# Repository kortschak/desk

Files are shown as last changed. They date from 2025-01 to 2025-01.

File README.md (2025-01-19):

# desk controller

This is the code and hardware details for a WiFi/Bluetooth Man-in-the-Middle controller for an AOKE Wistopht WP-CB01-901 32.5 standing desk controller.

The project is educational only. If you do not know what you are doing, do not use this document as a how-to. Using the device described here will almost certainly void your desk's warranty.

## Controls

### HTTP

The controller will be visible as `desk` in your LAN. It exposes HTTP endpoints.

Endpoints:
- `PUT /move_to/?position=<pos>`: `<pos>` is `1`, `2`, `3` or `4` corresponding to the programmed memory heights for the desk
- `GET /height/`: returns height of desk

Due to the protocol used by the desk, the height endpoint may return the last programmed memory height instead of the actual desk height.

### Bluetooth

The controller will advertise a service with your provided name and UUIDs. The `move_to` characteristic is read/write allowing you to move to the programmed memory heights for the desk, and a read `height` characteristic that will give a string showing the height of the desk. If the value is "0", it is not yet known to the remote controller.

## Building

Install `tinygo` version 0.34.0+ and then:

If building for HTTP control, write your SSID into wifi/ssid.text and your WiFi password into wifi/password.text. Do not add a final newline to the files.

If building for Bluetooth control, write single word name into a file advertise_name.text to name the Bluetooth service and then provide UUIDs for the service and exposed characteristics: `uuidgen >service.uuid`, `uuidgen >move_to.uuid` and `uuidgen >height.uuid` (confirm that the UUIDs do not collide with any that are already being used locally).

Use `tinygo flash` at the root of the repo with the target Raspberry Pi Pico W attached to a USB port:

- HTTP-only: `tinygo flash -target pico-w -stack-size=8kb .`
- Bluetooth-only: `tinygo flash -tags bluetooth -target pico-w -stack-size=8kb .`
- both: `tinygo flash -tags http,bluetooth -target pico-w -stack-size=8kb .`

Attach the handset to the Handset RJ45 socket on the board and a **non-crossover** Cat5 cable from the controller to the Controller RJ54 on the board. Provide USB 5V power to the Raspberry Pi Pico.

## Circuit

diagram

RJ45 pinout:

1. brown — Controller UART Rx
2. red — Controller UART Tx
4. yellow — button pressed (do action), also required during initialisation (16ms pulse to start communication)
5. white — GND
8. black — +5V

UART is 9600 baud.

## Protocol

The communication protocol used by the desk controller is based on 5-byte packets. The initial header byte distinguishes Controller-to-Handset from Handset-to-Controller packets, this is followed by 3 content bytes and then a single checksum byte.

The checksum byte is a literal checksum of the content bytes; 1st+2nd+3rd ignoring carry.

### Controller-to-Handset

Header byte: `0x5a`, followed by 3 digits encoded based according to the bits required to specify the segments of a 7+1 segment display.

7-segment display:
```
  -2-
|     |
5     1
|     |
  -6-
|     |
4     0
|     |
  -3-   7
```

Digits:
```
0 = 0x3f  0. = 0xbf
1 = 0x06  1. = 0x86
2 = 0x5b  2. = 0xdb
3 = 0x4f  3. = 0xcf
4 = 0x66  4. = 0xe6
5 = 0x6d  5. = 0xed
6 = 0x7d  6. = 0xfd
7 = 0x07  7. = 0x87
8 = 0x7f  8. = 0xff
9 = 0x6f  9. = 0xef
```

Additional codes:
```
R = 0x77
T = 0x78
E = 0x79
```

`E` is used for error codes, and `R`/`T` are used in conjunction with `5` to indicate reset.

Note that the encodings for `4` and `E` do not actually match the segments that are illuminated. ¯\\\_(ツ)\_/¯

This encoding [matches](https://web.archive.org/web/20211224215036/https://twitter.com/_kortschak/status/1474495857814769666) the [2021 day 8 Advent of Code problem](https://adventofcode.com/2021/day/8).

### Handset to Controller

Header byte: `0xa5`, followed by a zero, an button press coded as bits of a byte, a byte that ensures that the checksum will be `0xff`, and then the checksum.

Button encoding:
```
bit: 7654 3210
key:  DU4 321M
```

When a button is pressed, the yellow wire (line 4 of the RJ45 connector) goes high.

### Handshake

On start-up the yellow wire (RJ45 line 4) is made high by the handset for 16ms and then the handset and controller UART Tx lines are enabled. The handset then chirps a number of `a50000ffff` packets at 10ms intervals and waits for a controller response of a single `5a00000000` and then continued `5a<height><checksum>` packets. If this does not happen after some long period, the controller and handset appear to go into an error state.

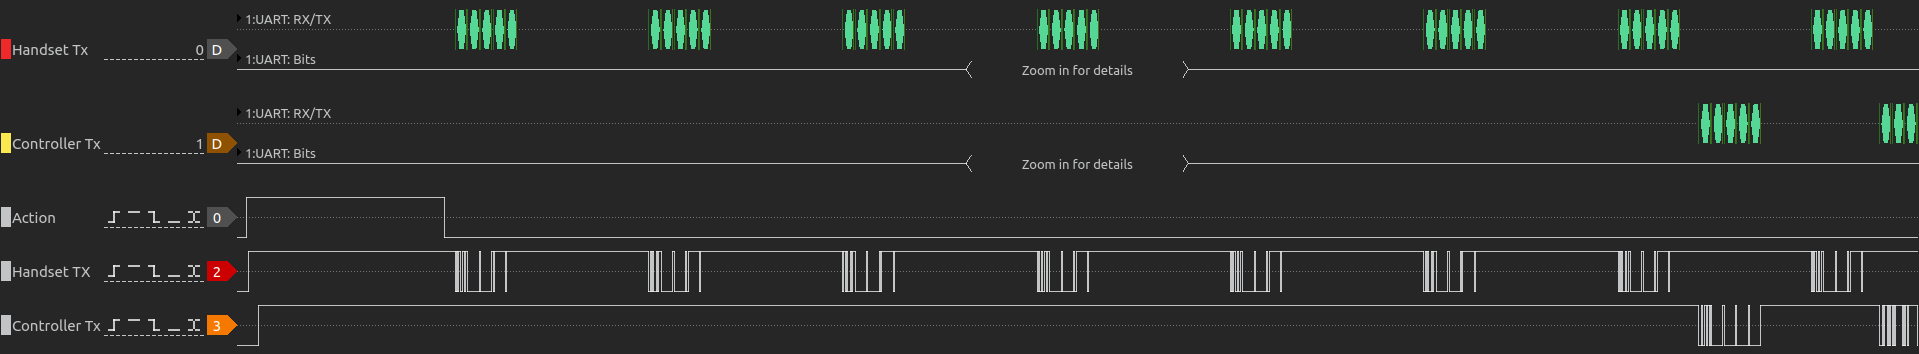
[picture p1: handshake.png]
handshake


### Watchdog

At 18 minutes after the last button action packet sent to the controller by the handset, the controller sends a single `5afffffffd` packet. After this, actions sent to the controller will fail with an E04 error. This can be reset by a physical handset button press, but not by packets sent by the remote controller. The issue can be mitigated until the protocol is more fully understood by chirping five `a500609fff` packets before the watchdog time elapses. This packet is a `du-----` button action; resetting the watchdog timer, leaving the desk in the current position and refreshing the remote controller's knowledge of the desk's height.

The watchdog shutdown sequence is a `5afffffffd` response by the controller to the handset`a50000ffff` query.

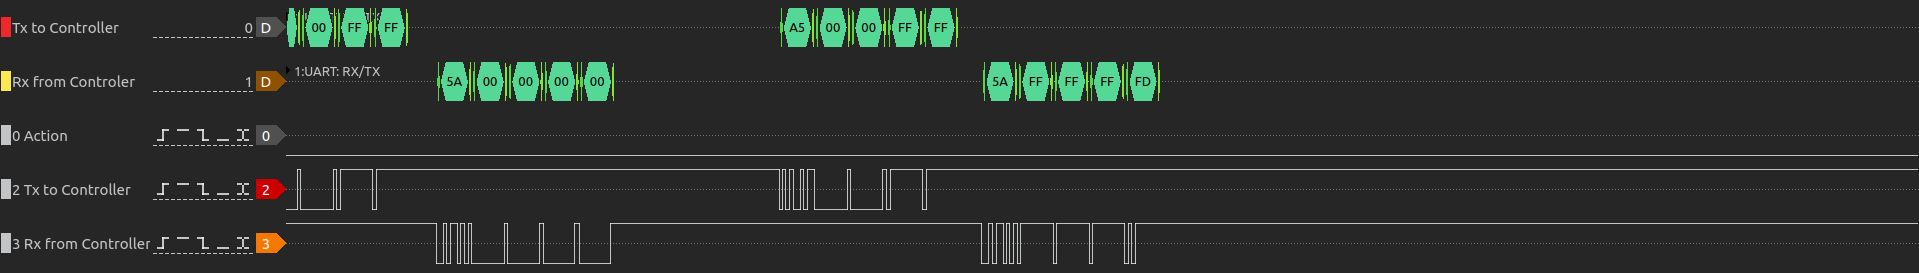
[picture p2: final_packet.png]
final packet


Then 200ms after the start of the response, the controller UART goes low, and 2ms later the handset UART goes low. A button press or handshake restarts the 18 minute cycle.

shutdown

## Limitations

The handshaking protocol between the linear actuator controller and the handset is has not been possible to properly implement for the handset side via the remote controller, so it is not handled at all. After power-up, it may be necessary to momentarily press a controller button and then wait for the display to turn off. After this, the remote controller will work.

The connection between the linear actuator controller and the handset carries +5V, but it does not appear to deliver enough current to support the remote controller. So power is delivered to the remote controller by USB.

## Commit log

2025-01-08 remove ineffective handshaking
    It seems that mimicking the the communication that's seen in the logic
    analyser trace is not enough; it appears that the handset needs to
    respond to communication from the controller and does not with the set
    up that exists, so remove it and directly wire the controller's RX to
    the handset's TX with a wire passthrough. This does not fix the issue,
    but reduces the amount of work that we were doing and appears to allow
    the system to re-handshake after a single handset button press and wait
    until the handset display blanks. The RX from the controller is retained
    so that the MitM is still aware of the desk height.
2025-01-08 update diagram for 2-socket design
2025-01-08 add gerber files for board
    [pcb-B_Cu.gbr, pcb-B_Mask.gbr, pcb-Edge_Cuts.gbr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]
